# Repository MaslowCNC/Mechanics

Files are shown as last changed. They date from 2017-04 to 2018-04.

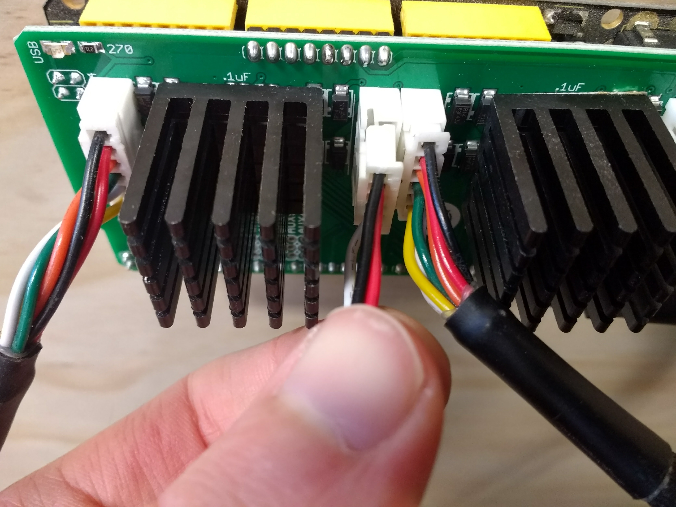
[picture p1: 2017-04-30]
Documentation/Installing The Z-Axis/Plug Into Controler.jpg

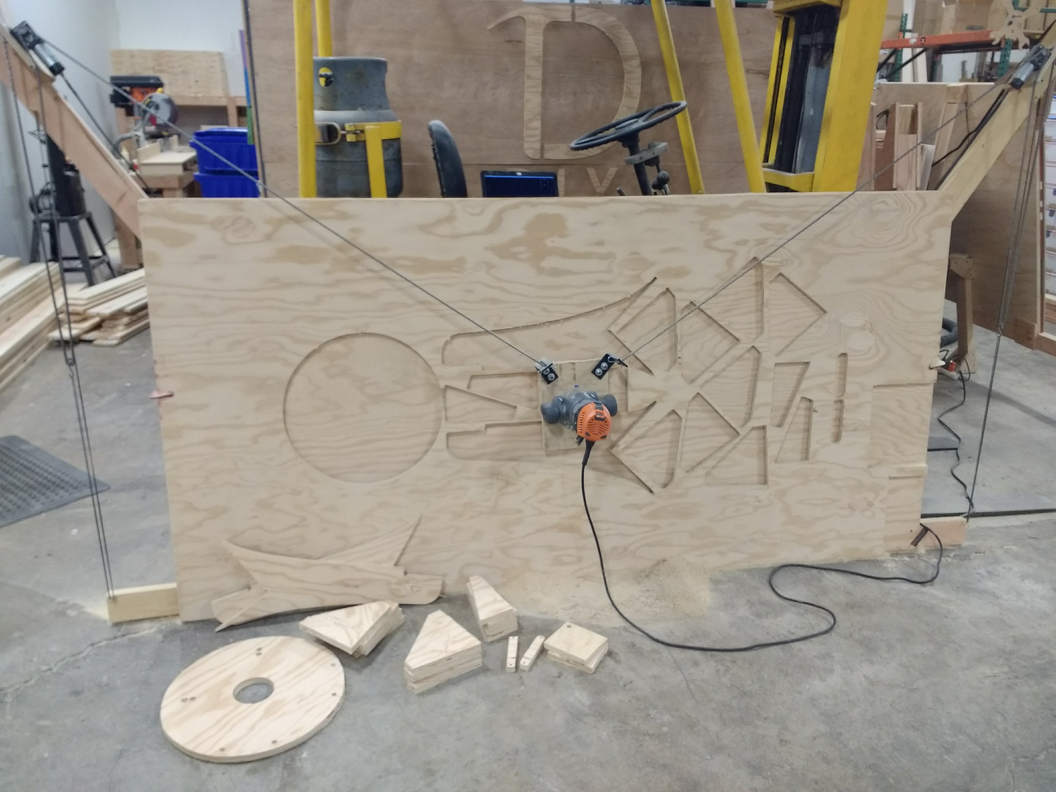
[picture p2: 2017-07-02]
Documentation/Cutting Parts With Temporary Frame/All Parts Cut.jpg

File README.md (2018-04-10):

# Maslow CAD

The digital design files for the Maslow CNC Machine

===

Digital Design Files

The official latest version of the design has moved from Sketchup into OnShape, a web based
parametric CAD program which lets us more easily modify and adadpt the design than Sketchup
did. 

You can find the OnShape model for the default frame here:

[Default Frame OnShape Model](https://cad.onshape.com/documents/bb4070d4347a04156066aecd/w/cc700f50fb591efdcf3dff27/e/5fe97348d45b2bf22a29a1ce)

You can find the OnShape model for the bolt together frame here:

[Bolt Together Frame OnShape Model](https://cad.onshape.com/documents/541f931ef1cd300726f54cf3/w/2e46e46e415d8c274b77c05c/e/bbd5cb914ffed6d673f649a3)

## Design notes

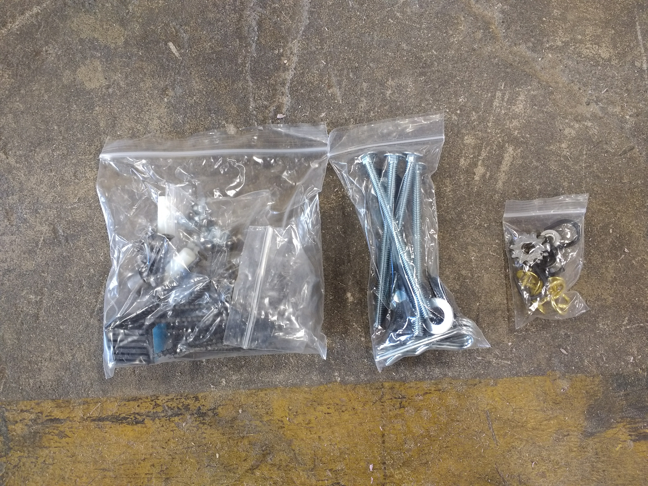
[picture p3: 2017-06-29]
Documentation/Hardware Bags.jpg

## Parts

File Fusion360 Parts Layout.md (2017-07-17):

# Unofficial Fusion360 parts file
---  
It was mentioned that the Autodesk folks might be making a post-processor for MaslowCNC (GC). In preperation for optimization of Fusion360 for use with MaslowCNC I've created and shared a Fusion360 Project that incorporates and extends the 'All_Parts_Laid_Out.svg' document, designed for cutting MaslowCNC from a single sheet of plywood, and hope to continue to update this Fusion360 Project file to allow easier creation of additional MaslowCNCs and to make it easier for folks to begin building and working with Fusion360 to design things to be built with MaslowCNC.

Experienced Fusion 360 users and/or active MaslowCNC Developers are welcome to contact me in order to be added as collaborators on this project within the Fusion 360 Cloud platform.
  
---
### [MaslowCNC Beta3 Parts](http://a360.co/2sV4YRd)
---
  
### Updated (7/7/17): 
* Parts Sketch, suitable for cutting all parts from a single piece of Plywood.
* Seperate 'extrusions' for each part
* Simple Component Paths: The Bare minimum to make the shapes and cuts necessary for the MaslowCNC parts. 
* Advanced Component Paths: All part paths, Pockets for the Sled mounting bolts, the Rigid Router's own plastic sled, engraved angle braces.
  
### To be added:  
  * More accurate machine settings (Feeds and Speeds) for all paths.
  * Roundover cuts for the Advanced sled, using a V-Bit
---  

More information: [Fusion360 with MaslowCNC](https://github.com/MaslowCNC/GroundControl/wiki/Fusion360-with-MaslowCNC)

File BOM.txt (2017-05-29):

Frame BOM:

8  x Cup Hooks
6  x 1.5mm Pullies
2  x S-hooks
2  x Idler Sprockets
2  x Drive Sprockets
2  x Motor/Gearbox/Encoder (291:1 reduction gearbox with worm gear to prevent back driving motor, 30kg/cm torque, 20 rpm, 12 volts)
2  x Motor Mounts
2  x 2.5"x3" U-Bolts
2  x Chain Brackets
2  x Chain Bracket Bolts
4  x Cotter Pins
25 x Wood Screws
3M x Stretchy Tensioning Cord
2  x 11' #25 Roller Chain

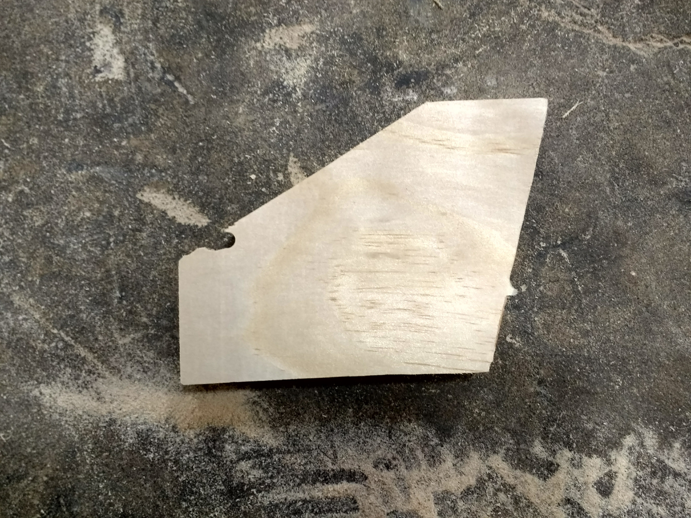
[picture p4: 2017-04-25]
Documentation/Cutting Parts With Temporary Frame/Part With Gash.jpg

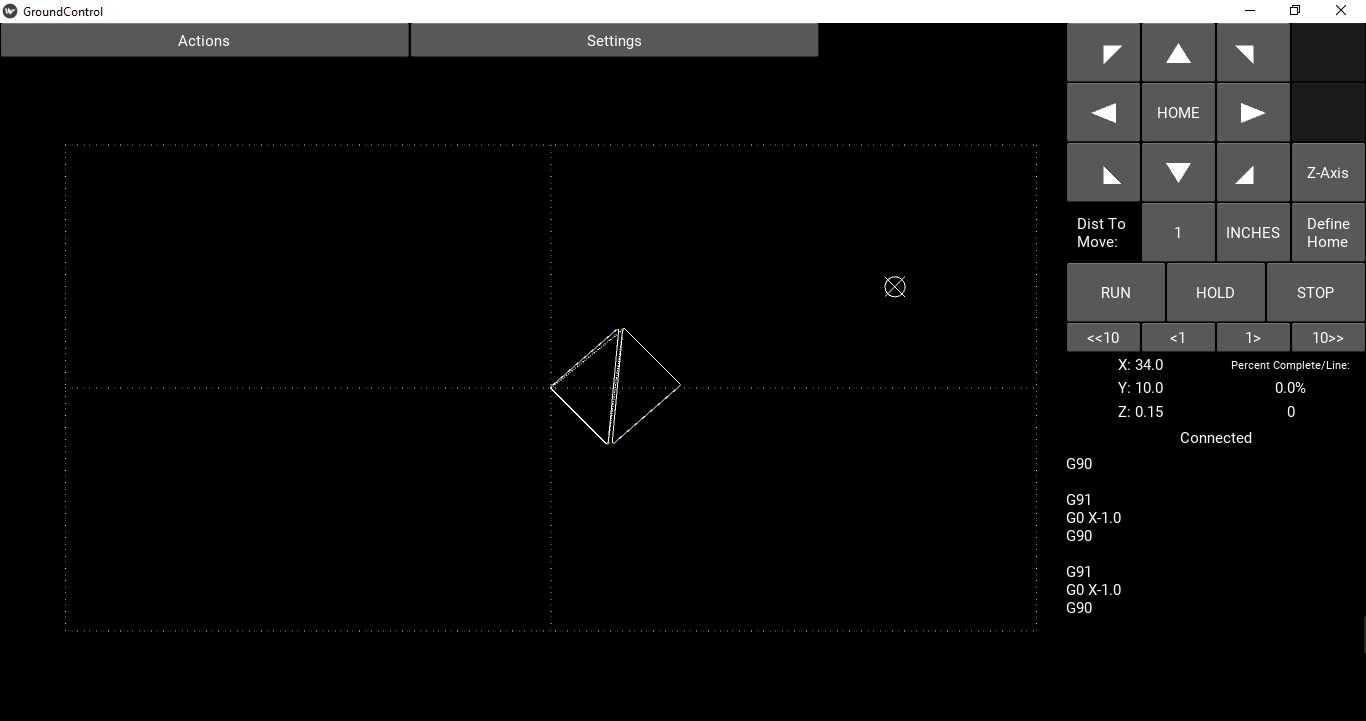
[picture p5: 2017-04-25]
Documentation/Cutting Parts With Temporary Frame/Move Machine Over.JPG

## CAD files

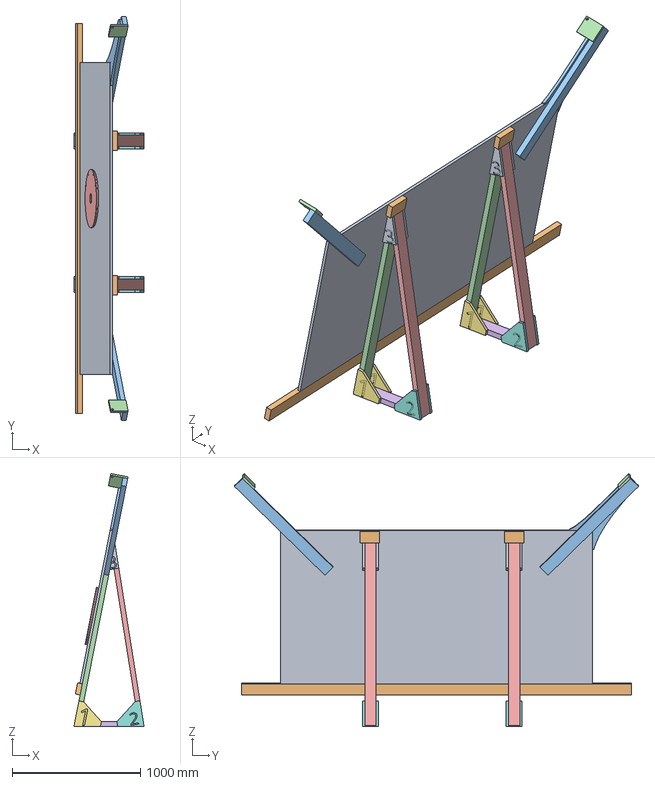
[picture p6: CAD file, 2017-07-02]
Maslow Frame.step
548.2 x 3156.8 x 1976.4 mm

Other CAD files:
Hardware/Bracket A.skp
Hardware/Bracket B.skp
Hardware/Bracket C.skp
Maslow Frame.stl
Maslow Frame.x_t
Testing and Calibration/6 Inch Square Test Shape.skp

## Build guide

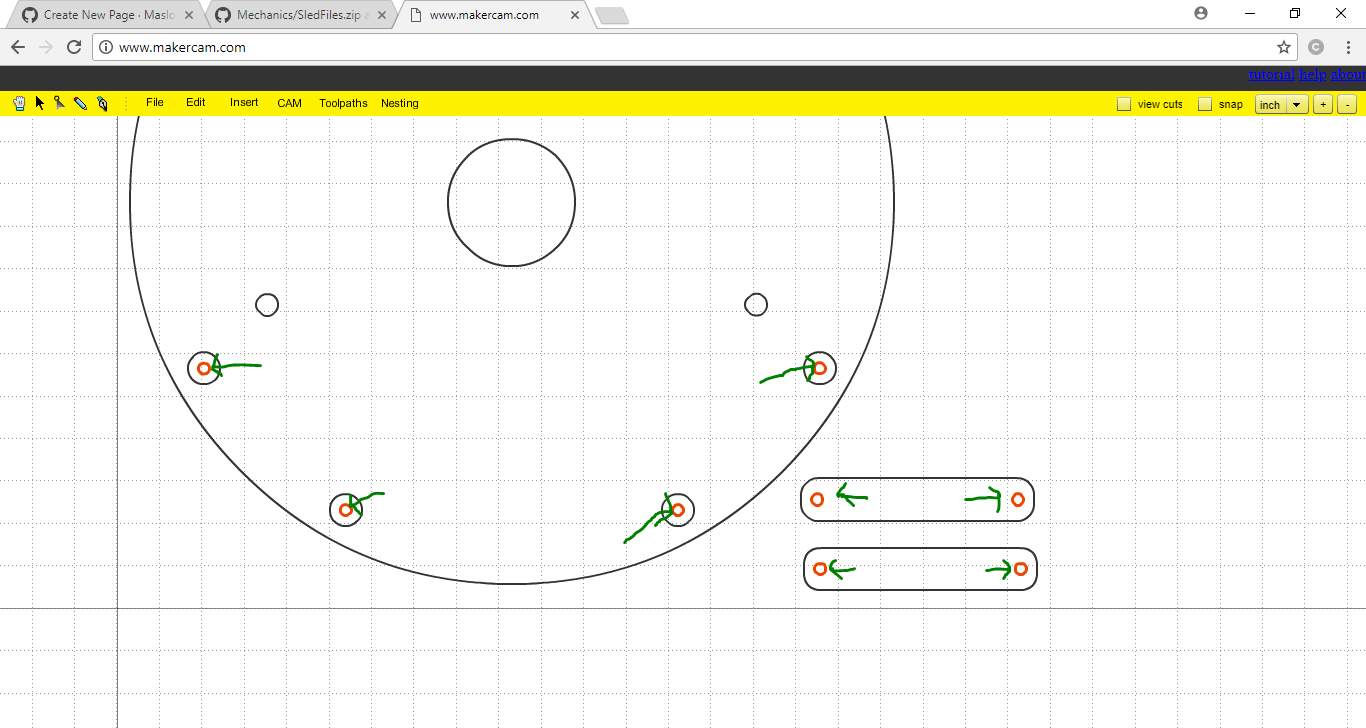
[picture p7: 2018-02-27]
Documentation/MakerCAM/Eight holes.PNG

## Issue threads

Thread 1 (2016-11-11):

Motor/Gearbox/Encoder - Specific Requirements

iceblu3710, 2016-11-11:
What are your requirements for the motor?

* RPM at shaft
* Running torque
* Min effective CRP at shaft

NeoTheFox, 2017-04-01:
Yes, some details would be nice.

mrfugu, 2017-07-13:
motor details have been documented.
this issue probably can be closed.

Closed 2017-07-13.

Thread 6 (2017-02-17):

Make motor placement more defined

BarbourSmith, 2017-02-17:
Where to place the motor on the motor mounts is a little unclear. I would like to add recesses for the screws to indicate where they should go and a second hole which the chain passes through after going over the sprocket to encourage consistent placement.

blsteinhauer88, 2017-03-29:
Awsome idea!

mrfugu, 2017-07-13:
New Arm Design appears to resolve this.

Closed 2017-07-13.

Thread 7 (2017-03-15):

Motor_Mount.svg file seems wrong.

blurfl, 2017-03-15:
MakerCam and InkScape don't seem to find an outline in the file. Was it created from the appropriate view?

blurfl, 2017-03-15:
Here's a file that looks OK in MakerCam and InkScape.
[Motor_Mount.svg.zip](https://github.com/MaslowCNC/Mechanics/files/846039/Motor_Mount.svg.zip)

mnelson78, 2017-03-15:
I opened it in Illustrator and it looks good now.

BarbourSmith, 2017-03-15:
Does PR #8 look like it fixed the issue?

blurfl, 2017-03-15:
MakerCam is happy with them all. InkScape sees the stroke as 90px wide, so renders them with hugely fat lines :(
Should there be one for the sled, as well?

davidelang, 2017-03-16:
when doing CAD work in .svg (inkscape and others), you should always use an
extremely thin line, otherwise you run the risk of the machine trying to cut
both sides of the line.

On Wed, 15 Mar 2017, Scott Smith wrote:

> MakerCam is happy with them all. InkScape sees the stroke as 90px wide, so renders them with hugely fat lines :(
> Should there be one for the sled, as well?

BarbourSmith, 2017-03-16:
@davidlang I agree. The line exporter in sketchup doesn't seem happy exporting a line thinner than .05 in which isn't exactly narrow, but it is better than it was. I think I may need to download inkscape tomorrow to make them truly hair thin.

I've also added a file for the sled.

Do we feel good about merging PR #8 as is for now?

blurfl, 2017-03-16:
Bar,
 I’m using the .SVG exporter mentioned to Hannah by RifleSpiral , 20dThu Feb 23 2017 05:14:46 <http://www.maslowcnc.com/forums/#!/no-judgement:sketchup-is-friend-not-foe/theres-a-branch-on-github> and it is willing to do 3.54px (on the Mac I’m using…). No special setup, just using the 1mm defaults for line size.

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

blurfl, 2017-03-16:
Bar,
The motor_mount.svg file was not updated with the rest of them, it is still the fat one. Other than that, ready to merge.

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

davidelang, 2017-03-16:
It sounds like the right thing to do, so no reason not to merge the fixes

David Lang

k

BarbourSmith, 2017-03-16:
Thanks for the advice everyone. I'll make everything as close to zero width as I can first thing tomorrow. Yall are also welcome to make pull requests for this kind of thing if it's faster

Closed 2017-03-15.

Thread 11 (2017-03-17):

Missing SVG file for brick holding bracket on sled

mnelson78, 2017-03-17:
There is not an SVG file for the bracket that holds the bricks onto the sled, and there should be.

mnelson78, 2017-03-20:
Bracket is now posted.

Closed 2017-03-20.

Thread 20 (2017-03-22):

Reduce friction between sled and cutting surface

BarbourSmith, 2017-03-22:
I suggested in [this video](https://www.youtube.com/watch?v=5pmNkcbVRkE) that we need to reduce the friction between the sled surface and the wood being cut.

In the video I suggested that we could reduce the friction by pocketing out some of the area under the sled. It has been pointed out (very correctly) that friction has more to do with the weight of the sled, than it does with the surface area so creating a pocket can't actually reduce the friction. I think there is still some room to play with the idea of pockets under the sled for either improved dust collection or to distribute the weight differently because drag toward the edges of the sled produces greater torque to twist the sled than drag near the center.

The two factors which affect friction are the coefficient of friction and the weight of the sled.

We can reduce the coefficient of friction by using a slippery material like nylon or HDPE to make our sleds. I think that's a fantastic idea, but since it's not available to everyone I'd like to look for other solutions in the meantime.

Reducing the weight of the sled is a good option. We don't really need to reduce the weight, only the force excreted by the sled on the material being cut, which we can control by adjusting the tilt of the machine. The current angle was decided back when we were using a much smaller less stable sled. I think our new larger sled could handle a much lower angle and still be stable.

davidelang, 2017-03-22:
I've been wondering about the angle, I figured I'd ask the beta testers to do
some experimentation with steeper angles once we started getting several of them
online.

That should let the sled be lighter as well (while keeping the same tension on
the chains), which would also open up the possibility of faster movements for
the design (either via motors with different gearing or larger sprockets)

mikberge, 2017-03-25:
first thing it come my mind, something cheap and easy to find....one cutting board! made with plastic similar to nylon or teflon .made to be durable and glide well. i think about two option , same form as the sled or many pocket under the sled plywood to insert many disc of cutting board strategicly these kind of plastic can be cut with the maslow

mikberge, 2017-03-25:
https://www.walmart.ca/en/ip/mainstays-pp-cutting-board/6000196138411

davidelang, 2017-03-25:
or this one that was posted a while ago

https://www.samsclub.com/sams/bakers-chefs-commercial-cutting-board-15-x-20/126035.ip?xid=plp:product:1:1

k

Seventhram, 2017-04-02:
Hi, I'm a beta tester.  I'm in the process of building my frame. I was a little concerned about the angle as well. I built my frame to be adjustable (using bolts on the top and bottom). Currently I have mine built to a 15 deg angle. I like the cutting board as a sled idea. I purchased a walmart cutting board, its rectangular, 20"x15"x3/8"thk. I'll most likely cut it to be more of an elliptical shape. Pic's to follow.

BarbourSmith, 2017-04-02:
Let us know what you learn!

buzz4209, 2017-04-03:
Many woodworking projects use melamine coated plywood or OSB for reducing friction. It's cheap and readily available.  Chamfering  the edges should be done too, as sharp corners may have a tendency to dig in and catch on any roughness present in your materials.

The cutting board idea is a good one, but I'm not sure the 1/2 inch thick polypropylene ones will work out long term. I'd worry about rigidity and durability based on the ones I have in my kitchen. :-) Best would be Corian (countertop type material) it's harder and slicker. Polypropylene will wear (scratch) much more readily than corian or melamine. It's generally a softer material. Unfortunately the Corian cutting boards are harder to find. I think Menards in the US often has them.

rb0087, 2017-04-08:
I think that ball transfer bearings would be the ideal solution to this problem, but it would potentially add a bit to the cost. Still, I think that it's an idea worth considering, because it would eliminate the issue of sliding friction with the wood. Instead, you would have rolling friction with the wood, and mostly rolling friction between steel ball bearings inside. The issue of it catching on the edges would also be largely eliminated. I think that you could source suitable ones for around $2 each in bulk, and if the design used ~10 of them, it wouldn't be a huge expense. It's also quite possible that some creative minds could think of a cheaper alternative that's inspired by this. Other than cost, the complication with this idea is that you would need enough of these to make sure that previous cuts in the plywood don't cause problems. If you had a perfect surface, 3 would be enough, but it would obviously cause problems if any of the 3 were going over dips in the plywood.

With the current design, regardless of what material the base is made out of, or what shape you have, with a flat base bearing on the surface, you'll still have sliding friction, and it will be difficult to predict because one of the materials is obviously plywood. Moisture content of the wood, the species/grade of the wood, etc. will all have an effect. When you have wood-wood, and wood on many plastics, you'll also see stick-slip behavior, which will make the motion difficult to control smoothly. This paper has some great info on the subject: [http://catalog.lib.kyushu-u.ac.jp/handle/2324/23785/p147.pdf](url) .

Also, if you do continue down the route of using a solid base like you currently have, I'd just like to point out that the shape does matter, regardless of the fact that you won't see the surface area anywhere in a simple friction equation. If this were lying flat on a table, and the forces were being applied right at the base, it might not, but in this case, the reaction forces at different points on the base will be different depending on how hard the chains are pulling (which will be applying a moment because the forces aren't directly in-plane), where the CG is, what the cutting force is and at what depth, what the grain direction is and what local imperfections are present, etc.  With uneven reaction forces comes uneven friction, which could be higher than a simple F=mu*m*g*sin(theta) would give you, and could be causing the base to rotate about its' center of gravity, which would cause positional errors at the cutting bit if it isn't the center of gravity.  Anyway, my main point is that it's not a simple situation, so I would trust your intuition that the shape is important. I think there's probably a bit of performance that could be gained by optimizing the shape.

BarbourSmith, 2017-04-08:
Thank you for that clearly well thought out and on point answer. I agree with everything you said.

The idea that the shape matters is I think an especially important one. The shape is a variable that we have a lot of flexibility to play with. We have the ability to play with not only the perimeter shape of the sled, but also the contact surface area by creating pockets.

The paper is quite insightful. Thank you for linking that. I thought that this graph which shows the "stick-slip" behavior of different plastic types was particularly interesting:
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
davidelang, 2017-11-14:
On Tue, 14 Nov 2017, Josh Martin wrote:

> For slickness, laminate flooring is cheap, or some self stick vinyl sheet would be ideal.

or UHMW plastic (available as cutting boards cheaply)

> Ball bearing casters can be had quite cheaply (~$1 on amazon) and come in nylon and steel. They can be inset from the bottom to minimize height.

they will have a tendency to fall in to areas you've already cut.

> Add a few coats of urethane to the bottom of your sled?

yes

> An air hockey table sled would be cool? (reverse your vacuum, it doesn't work that well anyway :P).

would be very cool.

> Remove the weights, add a bungee to the bottom center of the frame to the sled, and tilt the machine more.  It should provide comparable stability for cutting, but a better coefficient for movement.

see the discussion about adding a third motor that we had a few days ago, it
turns out this isn't nearly as easy as it sounds at first. When you are cutting
near the bottom corners, the bungee cord would be pulling in the wrong
direction, making a bad problem worse.

matthewkleinmann, 2017-11-15:
Some thoughts.  I don't have a router yet, but I have built a lot of things..

1) The ball bearings.  I am not a fan of this idea because as the piece the sled is gliding over starts to get tracks touted out of it, I would fear that unless the sled is perfectly balanced one or more of the bearings might get stuck or skip as it attempts to cross the void.

2) The cutting board.  I like the concept, but perhaps try making the sled out of aircraft grade plywood or even aluminum.  Yes, it is more expensive.

3) I am looking forward to hearing how the packing tape worked out.  Thin and inexpensive.  Perhaps that over aluminum as I think it would adhere better to a totally flat surface.

4) I worked on an experiment once and we bought thin adhesive backed teflon.  I don't recall the source or the price.  I suspect it was not inexpensive, but it was a really good material. and this use would only require a small amount of it.  Again, over wood or aluminum.

5) My last thought, more out of the box and harder to effect would be to make the sled something like an air hockey table powered by a shop vac.  This would give you some degree of weirdness in the Z axis, but I suspect for the vast bulk of the projects people are building with this router, that is acceptable.  For the things I would like to build, the Z axis is pretty much in or out.  FWIW, I got enamored with the air hockey idea pondering building extension feed tables for my planer.

davidelang, 2017-11-15:
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

This could also have problems going over earlier cuts (just like the bearings
approach)

servant74, 2017-11-15:
Another approach, is to use teflon.  Contact your local plastics supplier,
and get some thin Teflon or PTFE sheets that have been acid etched.
This will allow epoxy to attach well and stay.  Mix your favorite epoxy and
cover the sled bottom, and put on the sheet (etched side toward the epoxy)
and leave under some amount of compression (to keep things from springing
apart while the epoxy cures).
The sled can be cut/trimmed with normal tools to make way for smooth edges
etc.  Teflon is really pretty soft.

This was used when my Dad worked for Bell Helicopter on some of the parts.
They used high temp epoxy and put it in clamps then in an autoclave under
pressure.  But hey, it was for aerospace use, so money was no object.  We
used their cutoffs/scraps of Teflon like this to make furniture slides for
use around our home.  It worked well.

From a quick look online, the acid etched PTFE that is thin (say .02
inches) runs about $1.80/sq ft USD.  There may be minimum orders plus
shipping, but such is life ordering industrial goods.  Hopefully you can
find some without to much overhead involved.

davidelang, 2017-11-15:
On Wed, 15 Nov 2017, Jack in TN wrote:

> Teflon is really pretty soft.

I would worry that the Teflon will get chewed up by the edges of the wood and
chips (note that I worry about a lot of things)

matthewkleinmann, 2017-11-15:
David: On the air levitated approach, I had the same thought about the air levitated sled, but if you look at an air hockey table, most of the holes are uncovered most of the time.  For me the show stopper there is how complicated it is.

On the teflon, the stuff we had was tough.  It was akin to the stuff they use in dryer bearings.  Not quite that heavy but definitely tough stuff.

blurfl, 2018-01-10:
This is a valuable discussion, but not really an issue. Is there a way to move this to the forum or the
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

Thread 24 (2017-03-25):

Building temp frame step 10

sanenerd, 2017-03-25:
docs say
Step 10: Attach Cup Hook to top of Plywood Sheet

Attach 1 Cup Hook (found in the Small Hardware Bag) to the top left corner of the sheet of plywood below and slightly to the right of the motor shaft.

Pic show attaching to 2x4.. I assume photo is right

PS. I am sorry if I am putting this in the wrong place

BarbourSmith, 2017-03-25:
Great catch!

This is absolutely the right place!

The picture is correct, I'll change the text right now (you also have the ability to edit it directly using the "Edit" button in the right corner if you want)

BarbourSmith, 2017-03-29:
I'm going to close this if that's ok. I think it should be up to date. Thank you again for pointing that out!

Closed 2017-03-29.

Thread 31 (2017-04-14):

Unclear router description and features

jbarchuk, 2017-04-14:
Re; https://github.com/MaslowCNC/Mechanics/wiki/More-Photos
Bar, your page with the Bosch router explains a lot and the pics are excellent but might be confusing to users. First, it doesn't include a specific model number. I managed to track it down by the nameplate pic but there might still be oddities. These manufacturers build tools with different features and varying part numbers, and sometimes different features/numbers for different world regions.
Second, more importantly, is that the first pic might be misleading. That router is AAMOF the only one I've seen that has 'fixed base adjustable height' AND plunge style 'travel stops' features. It does that by giving the adjustment rod a latch mechanism that slips into the rotating 'stops wheel.' A user might see that wheel, see it on another router, and not understand the lack of the notch at the bottom of the adjustment rod, and get a router that can't do what's needed.
I think those pics should be moved to the 'router reviews' page with an explanation that it's a 'dual style' router suitable for Maslow's needs but unusual/different from other routers.

GeroBH, 2017-04-15:
@jbarchuk All pictures was originally here:   https://github.com/MaslowCNC/Mechanics/wiki/Tested-Routers-List
I admit, too many pics. Will try to make that more compact. They were moved to 'More-Photos' to make the router list better to overview.
Behind the model number there, it is mentioned that this router is not recommended and not tested. The 'not tested' will be removed today, because it is moving and it will cut. The 'not recommended' will remain, as this is one heavy beast (7kg without bricks and sled), to high, bringing the centre of gravity far over the sled. Moving it to the top edge of the cutting sheet made one of my motor mounts bend and a chain jump over the sprockets. It is sure not in the line of the goal 'Make it possible for everyone to have a Maslow', more on the line of testing how far you can go to reach the limits of the design. May I add more pictures of how the Z-Axis is mounted?

BarbourSmith, 2017-04-16:
I think more pictures clarifying how the z-axis is mounted would be a great thing. I think @jbarchuk is right that we should make it clear that it's a unique router type. @jbarchuk do you think it would be possible to make it clear without adding more pictures, just to keep the router review section clean? Hopefully we will soon have a number of routers listed there and I'm worried about it becoming crowded.

jbarchuk, 2017-04-17:
I didn't mean to give the idea that there were 'too many' pics. Absolutely
not at all. The more the better especially around the z-adjustment
hardware! Beyond that all these routers are just a motor and base.On one
level, there are two kinds of users. The first user has a router and needs
to decide if it'll work for Maslow. The second kind has particular projects
and needs in mind, and needs to pick a router.
On another level there are similarly two kinds of users. One (me for
example) has a very narrow-specific task, and they need to pick the router
with the best features for that task. The other user has potentially many
different kinds of projects in mind, has no router at all, and needs to
pick one with a wide enough range of variables that could meet all of those
tasks. For those folks there's more compromise required because there will
be no 'perfect' router.
There's no way to describe, show, and test every router on every material
under every condition. The best a web page of pics and descriptions can do
is say 'it does [this] really well and [that] average to poor.' It's up to
the individual user to decide if what they have will do what they need, or
which one they need to get to do what they need.
Again (heeere we go again :) ) this is where m00t and wiki are -not- good
software for these kinds of displays, descriptions and discussions. Yes,
one huge long page that has every photo and detail of every router can do
it, it's just -easier- to read one page about one router and not have to
bother with the others.
-More- information can -never- be a bad thing!!
Heck the 'too big too heavy' thing that you experienced Gero might be a
deal -maker- for someone who wants to drive a 1" bit through 1" oak!
Whether the -frame- is a little too weak to handle the high end of the
power bell curve is a different issue, but it's exactly those kinds of
tests that that user wants to read about. It's -very- easy to make the
frame stronger if necessary, and the chains and motors are certainly
already strong enough. As has been seen the exact frame build style is not
cast in stone. The intent of the Maslow concept is not 'this design can do
any and every task,' but that it can be tweaked and recast to do many
different specific tasks.
A related topic, whether the style of g-code generation of a particular
software, and exact firmware operation is suitable for any task is up in
the air. It's possible that there will be different power ranges that one
style works best for lightweight stuff and a different style works better
for heavy stuff.
This is all very similar to how plain router (or any power or unpowered
tool) operation works in real life. It takes practice and experience to
make any tool perform a task. Folks want to read about specific experiences
to see if things will perform nicely for what -they- want to do. If a
router is out of the range of what a user needs they'll have to decide if
the tweaks will be enough to bring it in range whether it's shallower cuts
or slower cuts or a different kind of bit or even a different frame angle.

On Sun, Apr 16, 2017 at 2:19 PM, BarbourSmith <notifications@github.com>
wrote:

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

GeroBH, 2017-04-17:
Thank for the comments. I could add something like a watermark with model and type on the picture itself, like GOF 2000 CE / Fixed Base. What do you think?

BarbourSmith, 2017-04-17:
I think it looks great. I didn't realize how big that router is until seeing the z-axis attached. Wow, it's huge! Overall, I think that the changes look great. Thank you for the update.

mrfugu, 2017-07-15:
I gave each router their own wiki page linked from the 'tested routers' page, this issue can probably be closed.

Closed 2017-07-17.

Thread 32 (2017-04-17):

Front Arms point needs rounding

mnelson78, 2017-04-17:
The front arms file goes to a sharp point.  This is the point that sits on the top of the sheet of plywood and points horizontally.  When cut out in plywood the point just chips away.  This also creates a weak point that is easily broken during the building of the arms.  I suggest rounding this point, perhaps a 1" radius?

BarbourSmith, 2017-04-17:
Great suggestion and an easy change

mrfugu, 2017-06-21:
I'm happy to make this change to the Fusion360 file I've created (http://a360.co/2sLJASm).

If you'd like, I can round that corner over and export out to a new Arm_Front.svg as well?

BarbourSmith, 2017-06-21:
@mrfugu, that would be great if you want to take that on! 👍 👍

I've been working on a frame redesign that dramatically reduces the part count and I just updated the github with the new versions of all the files so be sure to work from the latest files so we don't waste your time.

Cool Fusion model!

davidelang, 2017-06-21:
It's really nice with an update simplifies construction :-)

mrfugu, 2017-06-21:
Hey thanks, glad to assist.  I'll update the fusion project with your new SVGs 1st, then make any changes needed. will update once it's live.

mrfugu, 2017-06-21:
I've created Pull Reqs with the updated versions of 'All_Parts_Laid_Out' and "NewArmShape' incorporating a 3mm fillet to round over the sharp points in the arm, and widened the Brick Holder holes just slightly (from 6 to 7 mm) to allow Fusion360, in particular, to easily program those holes with a standard 1/4" plunge bit.

mrfugu, 2017-07-13:
this issue can be closed.

BarbourSmith, 2017-07-13:
@mrfugu  Thank you for flagging all of these

mrfugu, 2017-07-13:
no sweat. rock on!

Closed 2017-07-13.

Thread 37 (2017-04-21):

'Using the Temporary Frame to Cut Parts' has two Section 9's and no Section 10

blurfl, 2017-04-21:
Need to renumber.

BarbourSmith, 2017-04-21:
Great catch!

Feel free to edit the page, or I can take care of it first thing in the morning.

BarbourSmith, 2017-04-21:
Two 9's and no 10!

Closed 2017-04-21.

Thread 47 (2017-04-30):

Z-Axis Help

Seventhram, 2017-04-30:
Can someone please tell me which port to plug the Z-Axis cable too.

Can someone please post a picture of the mounting of their Z-Axis.

Suggestions on the best way to remove the knob and dial on a Ridgid R2200 router.

BarbourSmith, 2017-04-30:
Great questions, thanks for pointing that there needed to be a clear guide to that process. There is now a guide [here](https://github.com/MaslowCNC/Mechanics/wiki/How-To-Assemble-The-Z-Axis).

Let me know how I can make it better. 👍

Closed 2017-04-30.

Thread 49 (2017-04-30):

Design braces to be shapes which can't be reversed

BarbourSmith, 2017-04-30:
When assembling the legs it can be hard to tell which way the braces go. This could be fixed by making them more distinct shapes than triangles.

mrfugu, 2017-06-21:
Similar to my response to Issue #32 , I'm happy to edit my Fusion360 file and export updated .svgs for Angle Braces 4 and 5.

mrfugu, 2017-07-13:
Angle Braces 4 and 5 no longer exist.
this issue can be closed.

Closed 2017-07-13.

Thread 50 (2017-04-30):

Make cutouts for bit in arms larger

BarbourSmith, 2017-04-30:
The cutouts to allow the arms to have interior right angles where the motor plates mount need to be made larger for 1/4 inch bits

mrfugu, 2017-07-13:
this issue can be closed.

Closed 2017-07-13.

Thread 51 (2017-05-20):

Chain link height

ronbutterfield, 2017-05-20:
Please add a note to step 18, that the height the chain is attached to the sled should match the center of gravity of the router/sled assembly.  This may need to be adjusted for cutting very thick or thin materials.

davidelang, 2017-05-20:
and ideally you want the chain to be straight, so you want the motors out far
enough for your 'standard' material (say an inch from the frame + what's needed
for the center of gravity for the sled)

BarbourSmith, 2017-05-23:
That's a great point, it should be clearer.

Feel free to edit the wiki page directly when you come across something like that, or I can.

blurfl, 2018-01-10:
Has this been accomplished? If not, volunteers? 😁

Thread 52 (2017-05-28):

Detailed specs for motors and encoders

rodrigogoncalves, 2017-05-28:
Hi, is the [BOM](https://github.com/MaslowCNC/Mechanics/blob/master/BOM.txt) the official specs of the parts used? I'd like to know the makes and specs for the motors and encoders. Thanks

davidelang, 2017-05-28:
the motors are custom built, they have a 291:1 worm gear with a 7-line encoder
on the motor, resulting in 8148 pulses/rev of the output shaft, they have a
final drive torque of 30Kg/cm and turn at 20 rpm

Enjoying28, 2017-06-06:
I wonder if we can make a machine with these materials.

GM4632-370 DC 12V 30RPM High torque Turbo Encoder Motor Worm Geared Motor Reducer Motor
http://a.co/6l5dS2B
Browning 25B10 Minimum Bore Roller Chain Sprocket, Single Strand, Steel, 1/4" Stocked Bore, 10 Teeth
http://a.co/3dT9nYc
25 Roller Chain 50 Feet with 5 Connecting Links
http://a.co/0Qzel3k
Makeblock MegaPi - Born to Motion Control for Maker and Geek
http://a.co/iL2OnRn
Makeblock Megapi Encoder/DC Motor Driver
http://a.co/3wgzsT6
NEWSTYLE 12v 30a Dc Universal Regulated Switching Power Supply 360w for CCTV, Radio, Computer Project
http://a.co/7Ea39eI

maybe would have to edit the step factor

davidelang, 2017-06-06:
looks plausable, I'll point out that you are driving three motors which take
<0.5A each, so your 30A power supply is drastic overkill

The motor's rated torque is less than the maslow motors, but the worst that will
happen is that this means you have to go slower.

there will probably be some software changes needed to make the software run on
that board (and it's not clear from the Amazon page how much flash is on that
board, so double check that there is enough space.

David Lang

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

mrfugu, 2017-07-13:
an optional/equivalent parts list has been created.
this issue can be closed.

Closed 2017-07-13.

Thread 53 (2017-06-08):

All_Parts_Laid_Out.svg AngleBrace1 error

mrfugu, 2017-06-08:
In the file "All_Parts_Laid_Out.svg" the patterns (2) for the part called 'AngleBrace1.svg' has a sub-mm inconsistency in its long sides.

This doesn't seem to exist in the "AngleBrace1.svg' file itself, just the "All_Parts_Laid_Out.svg" file. It's minor, but probably adds unnecessary complexity to the tool paths generated for this part using this consolidated file.

-mrfugu

mrfugu, 2017-06-08:
Correction: This error appears on the long 90 deg edge of the AngleBrace1 shape, which appears 4x in the " "All_Parts_Laid_Out.svg" file

BarbourSmith, 2017-06-08:
Good catch! Thanks for noticing that. If you want to make a pull request which fixes it, I would love to merge it. If not I'll look into correcting the issue.

mrfugu, 2017-06-08:
Cool, will do it now.

mrfugu, 2017-06-08:
this is my 1st Github contribution, apologies if I made a mess of it.

mrfugu, 2017-06-08:
Well, the file is in my post, but it reads to me like i requested a merge of recently changed files as well, not my intent.

BarbourSmith, 2017-06-08:
😀 You ARE helping!

It seems like maybe a bunch of other files got wrapped up in the pull request for some reason, maybe give signing [the guest book](http://www.maslowcnc.com/howtocontribute) a go to test the process out

mrfugu, 2017-06-08:
Hey, thanks!

	Sorry about that, I’ll read more instructions before any future contributions, hope I didn’t make too big of a mess!

	Cheers,

Robert Crecine
429 1st Ave
Suite 8
Pittsburgh, PA 15219
412-580-8618

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

BarbourSmith, 2017-06-08:
The beautiful thing about Git Hub is it's virtually impossible to mess anything up. Every change is logged and reversible so you can pretty much always go for it! 👍 👍

mrfugu, 2017-06-19:
Ok, I think I got it right this time, I re-submitted the corrected 'All_Parts_Laid_Out.svg' file.

BarbourSmith, 2017-06-19:
Just merged it. Fantastic work! Thank you.
👍 👍 👍

Closed 2017-06-19.

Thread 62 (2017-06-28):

All parts SVG missing parts

ladyhawke13, 2017-06-28:
Shame on me for not going through the step of verifying - the All parts laid out SVG is missing the back piece of the arms, as well the two middle angle braces(the non-triangular ones). Also missing the SVG for those individual parts.

For non-beta users a measured diagram with all plywood and 2x4 parts numbered would be very helpful(speaking as someone who used to help with flat pack assembled furniture instructions!). I'll be winging it with scraps and likely using my jigsaw for the back arm piece, as I'd started disassembling my temporary frame before realizing that I was missing things.

BarbourSmith, 2017-06-28:
You caught me right in the middle of re-writing the instructions to not need those parts.

The new simplified design uses a 2x4 for the back of the arm part, and removes the middle brace from the legs to simplify construction.

I'll be re-writing the written instructions and taking pictures today.

ladyhawke13, 2017-06-28:
Leave it to me to pull at the wrong time! I have the frame supports together well enough, I just need to do the arms. I'll be retrieving my jigsaw from a different project site tomorrow and hopefully can get those cut out Friday.

BarbourSmith, 2017-06-28:
The new arms are mostly 2x4s, with the face plate mostly there for decorative reasons, You can really just use the 2x4s without bothering to cut the front parts if you want.

It will be more clear once I get the instructions written 😀

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

ladyhawke13, 2017-06-29:
Ahh, gotcha! I definitely have more than enough 2x4 scraps floating around to do that. I have the front pieces of the arms, just not the back. So easily enough sorted :)

mrfugu, 2017-07-13:
this issue can be closed.

Closed 2017-07-13.

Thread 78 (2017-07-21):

Source for Motor mounts

JDogHerman, 2017-07-21:
In the BOM I don't see a source for the motor mounts. Anyone have a suggestion where these can be acquired?

The measurements seem to have an opening of 28x40mm

JDogHerman, 2017-07-21:
I found a part that has a compatable opening.

I searched for

> GW31ZY GW370 DC Geared Motor Block Motor bracket Horizontal mount Motor Mount

Several showed up for less than $5.

Hopefully this will help someone else.

Closed 2017-07-21.

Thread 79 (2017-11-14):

Avoiding tearing down the temporary frame

skiz, 2017-11-14:
I was able to avoid removing most of the temporary frame (including all of the electronics, motors, etc) by taking a few precautionary steps along the way.  I have also avoided adding the additional arm facades, as I know my arms are both 20" out at 45 degrees.  I may revisit this at a later time, but it saved quite a bit of work and lots of recalibration time not having to deal with tearing everything apart.

1. Unplug anything that could move
1. Detach the sled (and z-axis if you have one), and use the pins to keep the chain attached on the gears (as close to the gear as possible).
1. Unhook the bungees from the tensioners, and safely remove and store the tensioners/hooks/gears.
1. unscrew the lower temporary legs as per the instructions
1. measure and screw the 2 6" blocks to the back/top of the frame.
1. build the permanent legs and mount per the instructions
1. simply hook back up the tensioners and remove the pins from the chain.

I figured this may save someone else some time, but being an "unofficial" hack, I'm adding it here.

BarbourSmith, 2017-11-14:
I am going to fully revisit the frame design and build process before batch three and I will try to incorporate these ideas, thanks for the tips!

blurfl, 2018-01-10:
Good suggestions, have they been incorporated? Is this issue needed as a 'to do' item?

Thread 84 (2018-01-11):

Why does the shop have a picture of z-axis mounted sideways on a motor mounting plate?

GeroBH, 2018-01-11:
Just curious and confused.
http://www.maslowcnc.com/store/z-axis
Middle picture
[https://static1.squarespace.com/static/57e561e720099e0d7a7f6aca/58276a5bf7e0ab81d3e577ae/589a5e20bf629ac702e0b122/1486596219084/Sideways.jpg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](url)

BarbourSmith, 2018-01-11:
In retrospect that is weird. Some routers have an adjustment knob on the side so the brackets are designed to work in both directions. As far as I know nobody has used that feature 🤷‍♂️

Closed 2018-01-15.

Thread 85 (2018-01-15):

Frame flex

BarbourSmith, 2018-01-15:
The stock frame has a measurable amount of flex in it which is becoming an important factor in calibration.

What is the easiest way to reduce the amount of flex in an existing frame while changing it the least amount?

blurfl, 2018-01-15:
I suggest a 10' 2x4 screwed to the arms just below the motor mounts as inexpensive and needing the fewest tools.

BarbourSmith, 2018-01-15:
Here is my first proposed solution:

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

It adds a 2x4 between the two arms. It requires an additional 2x4 and that the arm braces be re-cut, but no other changes are needed

BarbourSmith, 2018-01-15:
From playing with my current frame, there is some play between the motor mounts (the plywood which the motor is attached to) and the 2x4 that it is attached to. Is there any way to reduce play there? It seems like having both of the motors bolt directly to a long 2x4 is the best solution but a little bit harder to implement.

blurfl, 2018-01-15:
With  The motor mounts angled that way, there  could still be flex at the top of the work area. Turning them horizontal would allow you to screw them to the 10 foot 2 x 4, is that what you’re suggesting?

BarbourSmith, 2018-01-16:
I agree that we could still get flex at the top of the work area this way. I'm thinking that what we really want to do is what @dlang did where he moved the entire bar that the motors are on forwards so that the motors attach directly to the 2x4. I haven't thought of a way to do that which I really like yet

davidelang, 2018-01-16:
add a 10' 2x4 across the top connecting the wings. If you have the plywood  arm
covers, you can put the 2x4 in front of them and screw from the back.

This isn't the best new frame, but it's the quickest and easiest way to modify
an existing frame.

davidelang, 2018-01-16:
The best new frame is going to be very different from the best modification to an existing frame

modifying an existing frame is simply adding a 2x4, no need to modify the plywood parts

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

blurfl, 2018-01-16:
Adding the 2x4 in this manner helps brace the angled motor mounts as well - double win!

davidelang, 2018-01-16:
a top beam design that is similar to the original frame is
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

davidelang, 2018-01-16:
But I really like this folding, wheeled frame concept (and note that this makes it easy to move the top  bar forward)

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

all part of the onshape document at https://cad.onshape.com/documents/e635c24e358635f51da4b399/w/5a63b67113542f248fbe6d7b/e/50fff2211306b5f2bfa5dd3c

davidelang, 2018-01-16:
If we were willing to call a unistrut top beam the standard, we could have motor mounts made that would wrap around the strut and had a cap over the ends so that they were easily removable (with one bolt to hold them tight)

otherwise, you can just screw them to a 2x4.

Remember that the brackets don't have to be super strong, they need to support the weight of the top beam (~11 pounds for a 2x4) the sled (~20 pounds), the chain (~2 pounds), so call it ~25 pounds. That's not much and just about anything can do that without noticeable flex.

I didn't want to be screwing into the end-grain of the wood, so I already was planning for short lengths of 2x4 for the corners, so I just extended them to 12" long.

blurfl, 2018-01-16:
> call a unistrut top beam the standard

Before we do that we need to check in with users in other parts of the world... Steel strut might be hard to find and expensive outside the major urban areas of the US.

davidelang, 2018-01-16:
@blurfl

I agree, although unistrut is used for _so_ many things that it's probably available.

unfortunately, I can't figure out a good way to bend the material that would stay on the front of the material (so that it didn't care how deep it was)

blurfl, 2018-01-16:
@davidelang , I'm not sure I followed that...

davidelang, 2018-01-16:
2x4 is 1.5" thick, unistrut is 1  5/8" thick, pretty close to the same.

so if you have a motor mount that covered the bottom, end, front, and top of the beam, it would work with either unistrut or 2x material.

But I can't figure out something that's workable.

davidelang, 2018-01-20:
a note on the top beam attachment.

The alternate 1 design used a 2x10 on the top, with the idea that you can drill a series of holes in it and slide it forward an inch or two (a bit more if you use a 2x6 as the top board of the frame)

but a 2x10 is on the heavy side (heavier than a unistrut) and while this has some adjustability, it's not a lot.

So with the alternate 2 design, I extended the corner braces out so it doesn't depend on overlapping boards, which lets you use a unistrut or 2x4 for the top beam and move it to whatever distance you need. I made the supports 12", but it looks like 8-9" is about right for standard plywood.

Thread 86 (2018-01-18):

Wiki page claims 0.25in router bit but links to 0.1875in router bit.

abetusk, 2018-01-18:
The Wiki page for the [0.25in 2 Flute, Tungsten, Up Spiral Bit](https://github.com/MaslowCNC/Mechanics/wiki/0.25in-2-Flute,-Tungsten,-Up-Spiral-Bit) links to a bit sold on Home Depot that is in actuality a [0.1875in cut diameter](https://www.homedepot.com/p/Diablo-1-4-in-Up-Spiral-Router-Bit-DR75101/204073552).  The **Min Chuck Size Required** is `1/4 in.` but the **Cut Diameter** is `0.1875 in`.

I assume this bit should actually be a 0.25in cut diameter?  Could you please link to the proper router bit?

BarbourSmith, 2018-01-18:
Great catch! I vote we don't recommend that router bit at all anymore because there is a comparable one in our store for half the price. Although maybe it's a good idea to link to one that is available locally to most people. What does everyone think?

davidelang, 2018-01-18:
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

include both (with price/date fields that can be updated by users)

just listing ones you sell can leave a bad taste in people's mouth, even if it
is cheaper than the other one.

abetusk, 2018-01-19:
For people trying to build their own MaslowCNC, I think having a bill of materials that isn't tied to availability through the MaslowCNC's store front is a good idea.  Even if there's a primary link to the MaslowCNC's site with a secondary link to a comparable router bit on some other easily available site, maybe with a disclaimer, I think would be very beneficial.

People can decide for themselves whether they want to shop around for a cheaper or alternate router bit but providing a "known good" router bit helps in making that choice.  It's easier to tweak a known solution to an alternate solution than it is to create a solution from scratch.

abetusk, 2018-01-20:
Is this the actual bit that was used?

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

[0.25 in. x 1 in. Carbide Up Spiral Router Bit (2-flute, 0.25 in. chuck) ](https://www.homedepot.com/p/Diablo-1-4-in-x-1-in-Carbide-Up-Spiral-Router-Bit-DR75102/100660697)

If so, can we replace it in the Wiki?  There doesn't need to be a glowing recommendation to use this bit, but providing a link for a "known good" router bit goes a long way towards helping people trying to understand or assemble their own MaslowCNC.

BarbourSmith, 2018-01-22:
That looks like the right one. You are right that it's a good resource to keep, I agree with that reasoning

abetusk, 2018-01-23:
Wiki has been updated

BarbourSmith, 2018-01-23:
Excellent catch, excellent fix! 👍 👍 💯

Closed 2018-01-23.

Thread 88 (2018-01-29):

Broken link in wiki ("Z-Axis" page)

abetusk, 2018-01-29:
There is a broken link to a picture at the bottom of the [Z-Axis](https://github.com/MaslowCNC/Mechanics/wiki/Z-Axis) wiki page.

There is a picture of attaching a bungee cord to the router to take care of the slop and give more consistent cuts.  The picture was, as far as I can tell, originally posted to [the forum](https://forums.maslowcnc.com/t/z-axis-bungee-to-ensure-correct-depth/481).  There was a request to add it to the wiki, which was done, but the picture that was linked to has since rotted.

In general, maybe there should be a policy of linking, as much as possible, to pictures internal to the repo to avoid this type of link rot?  Could we add an 'img' folder somewhere so that the wiki can use that to point to images it needs?

BarbourSmith, 2018-01-29:
Great catch!

I've uploaded the image to the folder here: https://github.com/MaslowCNC/Mechanics/tree/master/Documentation

so the link will not break again. I agree that we should try to keep all our meda internal. I guess that would require pull requests to be made for pictures, but I think it's worth it

abetusk, 2018-01-29:
Thanks!

Closed 2018-01-29.

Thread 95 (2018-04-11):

Additions to Z-axis Kits

mrfugu, 2018-04-11:
Hey,

In running down the best solutions for reducing 'slop' in the Z-axis on the default system I think we have a list of materials well suited as additions to the Z-axis kit:

These are all low cost parts and readily available in quantity.

see: https://forums.maslowcnc.com/t/z-axis-only-moving-the-router-some-of-the-time/133/16?u=mrfugu

https://www.mcmaster.com/#91545a330
1-3x washers, used to remove slop from the bottom of the router screw in conjunction with retaining ring.

https://www.mcmaster.com/#98398a120
1-2x retaining ring, to replace/spares factory retaining ring, is possible to damage while placing washers.

https://www.mcmaster.com/#76445a743
12-18"x low friction tape. 3x router spindle body length. evenly spaced around router circumference

https://www.mcmaster.com/#12205t55
6x rubber bands. Works in conjunction with split-ring to apply down pressure on router in sleeve, between split ring and handle bolts.

https://www.mcmaster.com/#90905a659
1x split ring. sits on top of router head to hold rubber bands in place above router.

https://www.lowes.com/pd/Hillman-1-2-in-x-3-8-in-x-5-8-in-Nylon-Spacers/3012447
2x nylon spacers super glued on either side of router height adjustment flange. provides torsion stability to router part assembly:

 (640963002) Depth Interlock Lever
 (671758001) Depth Compression Spring
 (513396001) Depth Interlocking Lever Tab

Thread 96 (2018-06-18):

Flexible frame Concept

CMHinckley, 2018-06-18:
While it seems that there several posts asking if there are ways to make the operation of the Maslow CNC work in a more vertical orientation, it seems that a better solution might be to mount the frame directly to the wall with hinges at the top. The bottom would be pulled outward (and braced in this position for machining) and when machining is finished, the frame is rotated flat against the wall. This could eliminate a lot of framing, saving money, fabrication time and significantly reducing the storage space when the unit is not in use. Has anyone worked on a concept such as this, and would anyone like to work on such a solution?

The precision of the cnc machines can be influenced by dimensional changes caused by moisture and temperature fluctuations, the flatness of the bed, and the stiffness of the frame. It might be possible to increase the stiffness and stability of the frame by using a grid of 1"x 4" between 2 external layers (one front and one on back) of 1/4" hardboard sheets, which are flatter and cheaper than plywood. This composite frame could be formed by gluing and screwing parts together, and the screws could then be completely removed after the glue has set, eliminating every possibility of hitting a screw during machining. A sacrificial sheet, could be used in front of the machine frame to avoid damage to the frame when machining. Has anyone worked on a composite frame of this type, and would anyone like to work on such a solution?

davidelang, 2018-06-18:
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

you don't actually save that much, just the rear legs and kickers.

There are a number of people who have done this, and it workswell.

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

actually, most of the frame makes very little difference in the machine accuracy
(except if there is something that causes the sled to not slide, or the warpage
is bad enough to affect the Z depth)

The machine accuracy is almost entirely defined by how rigid the top beam is,
and how accurate the measurements during calibration are.

blurfl, 2018-06-18:
'''
mount the frame directly to the wall with hinges at the top.
'''
One of the beta testers, @Gero, built his fram this way, using a scissors jack to adjust the angle of the frame. It worked well for him.
'''
The precision of the cnc machines can be influenced by ... the flatness of the bed,
'''
I found this to be the case, the plywood I used for a workarea bowed and caused changes in the angle of the chain from the plabne of the sprocket. This would cause the chain to jump. It seemed to cause the sled to have additional frioction toward the sides of the workarea as well, but I don't have any data to prove it.

davidelang, 2018-06-18:
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

in your case this was inches worth of bowing to cause these problems

blurfl, 2018-06-18:
'''
in your case this was inches worth of bowing
'''
That's right. The composite frame that @CMHinckley suggests would be one way to prevent that kind of warping.

CMHinckley, 2018-06-18:
The max deflections of the top beam based on a total sled weight of approximately 17.5 lb (router, bricks, sled...) for the default frame is approximately 0.028" using Douglas Fir (Modulus of Elasticity of 1.8 million psi, and 2 x 4 framing). This includes the deflections resulting from the moment applied to the upright vertical members. This is a non-trivial portion of the target precision.  The best way to reduce the deflections is to increase the stiffness of the members and the bed.

blurfl, 2018-06-18:
That's true. Too, Doug fir is relatively strong but most users are using 'white-wood hem-fir' two-by lumber, which is less stiff and less stable.

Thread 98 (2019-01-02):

Different hardware than assembly guide/ videos

PoliciaMalo, 2019-01-02:
I finally got around to assembling my maslow cnc and there are hardware differences between the site instructions and what I received.

Is there an updated assembly guide for the new hardware?

Please...  I'm dying to finish assembly.

BarbourSmith, 2019-01-03:
Is the difference that you are missing the ring?

If that is the case I recommend using this linkage kit: http://maslowcommunitygarden.org/Maslow-triangulation-linkage-kit.html and then you can follow the normal instructions substituting the linkage for the ring. It will be a little bit more work, but you will get much better results than without the ring

PoliciaMalo, 2019-01-03:
No I have the ring kit and z axis.  It's hardware that I ran into after
mounting the motors

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

BarbourSmith, 2019-01-03:
hmmmm I am not sure what hardware that would be. Can you post a picture of what part it is?

PoliciaMalo, 2019-01-03:
Ahh ok I had to go to the instructions for the original design and the
parts were chain guides they changed the nails as well as added bushings
for the string pulleys.

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

BarbourSmith, 2019-01-05:
Excellent!

Can I ask how you ended up with the out of date instructions? Maybe I can
fix something to make them less confusing in the future.

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

PoliciaMalo, 2019-01-05:
The instructions on the website under the new default frame do not mention
the parts used in the old default frame.  Specifically the use of nails
instead of screws in the center bungee bearings, the use of nails now on
the center bearings instead of screws.  The small 2 inch plastil bearing
used in chain tension for the old default frame.  Etc.  I'll elaborate more
in the dorms when build complete.

Also the bungees seem too long compard to the photos in the new default
frame build.  I just ordered new bungee spool in case needed.

Thanks.

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

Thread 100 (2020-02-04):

Motor runs every time in same direction

mmmmmmmmmmmmmmm2, 2020-02-04:
Hi All please help me out, one of the motors is always running in the same direction, if i push up it goes up, if i push down it goes again up. and if i let it go to center it is every time somewhere else, and doesn't stop anywhere. what do i need to do...

JDogHerman, 2020-02-04:
Most likely the H-Bridge is dead on the controller card.

You could eliminate other remote possibilities that cabling  by swapping the Left and Right motor wires running to the card.

BarbourSmith, 2020-02-04:
I think this sounds like an encoder issue to me. If the motor can't read the encoder value it will always spin in one direction. What do you see happen when you press Actions -> Test motors / encoders?

mmmmmmmmmmmmmmm2, 2020-02-05:
Hi All,
tested the motors, it says testing L motor direction 1 Fail , direction 2 Fail, and that for L / R and Z
See attached photo, it is brand new, must be something i´m doing wrong

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

BarbourSmith, 2020-02-05:
Did you close the issue because you found the solution?

mmmmmmmmmmmmmmm2, 2020-02-06:
No i didn't, still not solve it ..

Pushed wrong button

Op wo 5 feb. 2020 23:14 schreef BarbourSmith <notifications@github.com>:

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

BarbourSmith, 2020-02-06:
Ok, let's figure out what is going on.

Do you see the motors move when running the test?

mmmmmmmmmmmmmmm2, 2020-02-07:
Hi all,

No, they do not move, when testing

But when i push manually it moves..

Op do 6 feb. 2020 23:34 schreef BarbourSmith <notifications@github.com>:

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

BarbourSmith, 2020-02-07:
Gotcha. When all three motors fail the test the issue is almost always with the power supply. Does the power supply have a blue light on it? Does the green light next to the plug come on when you plug the power supply into the controller board?

mmmmmmmmmmmmmmm2, 2020-02-07:
Good,

Correct, only two green lights.. no blue lights

Op vr 7 feb. 2020 07:14 schreef BarbourSmith <notifications@github.com>:

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

BarbourSmith, 2020-02-07:
Where are the the green lights? Are they both on the controller board? Can you post a picture of the controller board and the power supply?

mmmmmmmmmmmmmmm2, 2020-02-07:
See attached photos

One of controllerboard and of the adapter

Op vr 7 feb. 2020 17:36 schreef BarbourSmith <notifications@github.com>:

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

BarbourSmith, 2020-02-07:
I don't think the photos actually attached 😢

mmmmmmmmmmmmmmm2, 2020-02-08:
Mmmm, strange..

Will send them in 2 emails

Op vr 7 feb. 2020 23:01 schreef BarbourSmith <notifications@github.com>:

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

mmmmmmmmmmmmmmm2, 2020-02-08:
Number 2

Op vr 7 feb. 2020 23:01 schreef BarbourSmith <notifications@github.com>:

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

davidelang, 2020-02-08:
they did not come through, try adding them through the web interface.

David Lang

mmmmmmmmmmmmmmm2, 2020-02-09:
Okay, here they are
![Uploading 20200207_175711.jpg…]()

BarbourSmith, 2020-02-09:
I'm still not seeing the picture :(

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

Let's move this conversation into the forums...I think we'll have less technical trouble there, you will get faster responses from more people, and that is really the right place for the conversation since this is about solving a particular issue instead of proposing a change to the design of the machine

BarbourSmith, 2020-02-09:
The forums are https://forums.maslowcnc.com/. You can login with your github login so no need to make an account or anything

mmmmmmmmmmmmmmm2, 2020-02-09:
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
First

mmmmmmmmmmmmmmm2, 2020-02-09:
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
Second photo

BarbourSmith, 2020-02-09:
Nice! Ok everything looks good there. And we are still seeing the motor move when you manually command them to move, but no movement at all during the test?

mmmmmmmmmmmmmmm2, 2020-02-09:
Yes, no movement during test, but can do manual but always same direction

BarbourSmith, 2020-02-09:
This is totally like anything I have seen before. The test should be overriding the controls in a way which makes the motor move if it has power...but the pictures and the fact that you can manually move it mean we have power

BarbourSmith, 2020-02-09:
Is the behavior the same on all the motors? The only thing I can think could be a bad connection in one of the connectors. Maybe let's try unplugging them all and re-plugging each motor very firmly

mmmmmmmmmmmmmmm2, 2020-02-09:
Strange isn't? Is an idea to set up software again?

BarbourSmith, 2020-02-09:
So strange 😲

It could be worth setting up the software again, but this feels like a hardware issue to me

BarbourSmith, 2020-02-09:
I think checking the connections on the cables is the best place to start. I would unplug each motor and re-plug them firmly

mmmmmmmmmmmmmmm2, 2020-02-09:
It is new bought it end December , coming 2 weeks i'm not near my cnc, if you have any suggestions please let me know

BarbourSmith, 2020-02-09:
Did you try unplugging and re-plugging the cables to the motors?

Have you contacted MakerMade? Do they have any suggestions?

mmmmmmmmmmmmmmm2, 2020-02-09:
Haven't tried to switch the motors but tried several times the connection. Have no idea who to contact assume there is some kind of warranty..

BarbourSmith, 2020-02-09:
They should send you a free replacement for anything which is not working...the tricky thing is I'm not even sure what to ask them for because I'm not sure what is going on. Maybe ask for a new arduino and controller board to be safe?

You can find them in the forums by posting your issue and tagging them as @makermadecnc they usually respond there pretty quickly

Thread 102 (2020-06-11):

Initial plunge off path

DJscreen, 2020-06-11:
We are cutting designs into 6x4 sheets of 6mm ply. The designs are 6" x 6" max and the cutouts are removed to create a lattice effect. There are two of the designs where the initial plunge through the material is about 2 mm off leaving noticeable "dings". We intend to experiment with 2 mm tabs at the relevant places and by inserting bulges into the svgs which will be manually finished later.

The panel svg was set up using Inkscape v9 and the nc file generated in Krabzcam which as far as I can see is an excellent replacement for Makercam

BarbourSmith, 2020-06-12:
Hmmmm my first instinct is that this could be play in the router. Which type of z-axis are you using?

Another possible option is to add a lead in to your cuts which makes it so that the router bit doesn't raise and lower right along the edge of the part like this:

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

I am not familiar with Krabzcam, but I know CamBam supports it and they have a free trial version that might be worth playing with

DJscreen, 2020-06-20:
Thanks for your suggestions. We may have solved it by plunging the bit half way through the ply, withdrawing to safe height and then plunging to final depth. We have been using a 6mm twin flute cutter and maybe it is too stressed plunging the full depth in one go.

BarbourSmith, 2020-06-20:
That makes total sense. Nice problem solving!

On Sat, Jun 20, 2020, 2:27 PM David Johnston <notifications@github.com>
wrote:

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

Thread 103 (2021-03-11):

Chain pull on setup.

alaskanalain, 2021-03-11:
On setup, the "measure chain" step kept pulling the chain until it stretched, the arms bent a lot and the motor eventually started to pull loose, if I didn't stop it I assume the motor would have burned out or torn loose. I beefed up the machine and now it's built like a tank.
With the other chain, as before, I manually pulled the chain so there was a bit of slack then started to measure again, following instructions exactly, but it still bent the arms. It stopped and went slack as it should but not in time, so now the other chain is stretched too.  Both chains now skip on the teeth every time I try to do the test cut.  One tooth is slightly chipped too as a result (not too bad).  I have chain guides but it still slips due to the stretch.  The motors simply did not turn off and slack when they should.  The many youtube videos I watched have confirmed this.

I am reasonably good with machines but this has me near tears after many hours.  **Can I please get some new chains**, this time I will just use a tape measure, the measurements from the machine pulling them tight didn't yield accurate results either.

I went through the setup many times since and looked at this from every angle and don't think it's something I did wrong.  I have a small CNC and had no trouble with that at all.  Bicycle chains stretch and those are thicker than this, I assume that is why others also sometimes have issues with skipping.
Please help, Thank you
Alain

BarbourSmith, 2021-03-11:
I couldn't agree more that the calibration process is confusing and very much needs to be improved.

Which version of the kit are you using (ie who did you buy it from)? The chains and gears should be strong enough to handle the forces involved easily so I would be somewhat suspect of the build quality.

Which software are you using for calibration? WebControl or GroundControl?

alaskanalain, 2021-03-11:
Ground control and I think the seller was "Maker Made".  I got the kit with Z control, not sure what model, etc. It's one of the newer ones probably, got it a few months ago.
It's well made but the motors didn't want to stop pulling, they did eventually but I don't think it should pull that hard, definitely straining every component, I could hear the creaking and motor strain sounds.
I don't think the chains are made for that, far less beefy than my chainsaw and yet the chainsaw chain stretches on first use, it's designed with that in mind, Bicycles too.
Thanks for that, any ideas?  Do I have to buy new chains? Can I just measure the machine?  I am not even sure where the test cut should be on the plywood.

BarbourSmith, 2021-03-12:
I believe that they have their own software that might work better for you than Ground Control. I believe it's called Makerverse? Ground is pretty out of date at this point.

You can manually measure, but it isn't usually accurate enough.

Maker Made (https://makermade.com/) would be the people to get in touch with if you want some new chains.

alaskanalain, 2021-03-12:
Thank you

On Fri, Mar 12, 2021 at 8:48 AM BarbourSmith ***@***.***>
wrote:

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

BarbourSmith, 2021-03-13:
Of course, although I don't know if I really helped much :)

For better help come hang out in the forums:
https://forums.maslowcnc.com/

You can probably find someone with a similar experience there who might have some insights.

Closed 2021-03-13.

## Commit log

2014-11-17 Case Added
2014-11-17 Files Added
    [Bed.DXF, Sheet1.DXF, Sheet2.DXF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]
2014-12-10 Added extra dremel mounts
    [ExtraBrackets.DXF]
2015-01-20 Changed file names to be more clear
    [MDFBasePlate.DXF, MDFPartsSheet1.DXF, MDFPartsSheet2.DXF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]
2016-10-09 Add Maslow CAD files
    [ExtraBrackets.DXF, MDFBasePlate.DXF, MDFPartsSheet1.DXF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]
2016-11-03 Added BOM
2016-11-03 update BOM
2016-11-03 Updated BOM
2017-01-01 move mounting holes
    [Machine.skp]
2017-01-18 sled re-design
    [Sled.skp]
2017-01-30 backups saved
    [Sled.skp]
2017-02-17 move motors forward 25mm
2017-02-17 extend motor mounts
    [Machine.skp]
2017-02-17 update hole spacing and size
    [Machine.skp]
2017-03-15 Fix motor mount and add files for angle braces
2017-03-16 make motor mount lines thin
2017-03-17 add legs diagram
2017-03-17 add how to cut 2x4 picture
2017-03-20 make mounting holes larger
    [Sled.skp, TempSeld.skp]
2017-03-20 add temp sled
    [TempSeld.skp]
2017-03-21 add mounting holes with room for counter sink and regenerate PDF
2017-03-21 true up crosses and add brick holder
    [TempSeld.skp]
2017-03-21 new cad files with full page used
2017-03-22 commit to switch branches
    [TempSeld.skp]
2017-03-24 put parts in order and switch inches to fractions
2017-03-29 Add hardware CAD models, organize
    [Bracket A.skp, Bracket B.skp, Bracket C.skp]
2017-03-30 regenerate temp sled svg
    [TempSeld.skp]
2017-03-30 remove brick holder part
    [TempSeld.skp]
2017-03-31 Update pictures for cutting frame
2017-04-14 Add picture of alternative frame
2017-04-17 Add a test shape to measure calibration
    [Test Shape.skp]
2017-04-18 Change test shape file name
    [6 Inch Square Test Shape.skp]
2017-04-20 Add picture of tuning calibration
2017-04-22 Forgot to include a second set of braces
    There are two legs. Duh
2017-04-24 Add missing motor mount to all parts laid out
2017-04-25 Add pictures of cut parts
2017-04-26 Add CAD pictures
2017-04-28 Add more photos for assembling the final frame
2017-04-29 Update leg diagram picture
2017-04-30 Add pictures for installing z-axis instructions
2017-04-30 Add attach bricks picture
2017-05-07 Add new machine design
    [New Machine Design.skp]
2017-05-07 Make dimensions more regular
    [New Machine Design.skp]
2017-05-09 Update design
    [New Machine Design.skp]
2017-05-10 update design file
    [New Machine Design.skp]
2017-05-12 Add new arm shape
2017-05-14 Add cut list for boards
    [New Machine Design.skp]
2017-05-29 Update motor specs
2017-06-18 Create All_Parts_via_Fusion360.txt
    Concept: to allow a new MaslowCNC user to easily begin working with Fusion360 by providing a 'comprehensive' Project file that includes extrusions for all machinable parts, discreet cutting paths, an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
2017-06-21 Change sketchup file names
    [Machine.skp, New Machine Design.skp, Old Machine Design.skp]
2017-06-21 Rounded the pointy ends of NewArmShape.svg
    Added a 3mm fillet to the pointy ends of the NewArmShape. (Via Fusion360, exported to Ai as .dxf, then exported to .svg)
2017-06-21 edit NewArmShape + allow 1/4" bit
    I rounded the pointy ends of the NewArmShape, and slightly widened (from 6 to 7mm) the Brick Holder mounting holes, in order to allow a 1/4" (6.4mm) bit to attempt to drill them. Fusion360 wasn't hap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
2017-06-28 Replacing invalid files
    I'm not sure why these appear as 'invalid' in the current version. The File size is significantly different from my local copies, so I'm reposting them via this pull req.
2017-07-02 Update CAD files
    [Machine.skp, Maslow Frame.step, Maslow Frame.stl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]
2017-07-03 Update final frame steps 1-8
2017-07-07 Updated to latest SVGs, new URL
    Rebuilt using the latest SVGs.
    New URL for Fusion360 Cloud project.
    Fusion360 File also incorporates the following changes:
    New GRBL PostProcessor
    Advanced tool paths for pocket cuts, and engraved angle braces.
    Refined Tool Settings and Tolerances.
2018-02-13 Add picture of bolt together frame
2018-02-15 Add cut list and drill list files
2018-02-15 add photos of cut parts
2018-02-15 Add pictures of holes drilled
2018-02-16 Add plywood spacers pictures
2018-02-17 add sprockets picture
2018-02-20 launch calibrate pic
2018-02-28 Add picture of cutlist for default frame
2018-03-01 add default frame CAD overview
2018-03-01 add photos for default frame
2018-03-02 update CAD drawing overview picture
2018-03-02 Update Cut List
2018-03-02 add picture of 2x4s cut
2018-03-02 add pictures through the legs
2018-03-03 Add pictures of frame built
2018-03-03 update CAD pictures
2018-03-03 update cut list with shorter motor protrusion
2018-03-07 Update CAD drawing images with latest design
2018-03-07 extend ledge to rest wood on .25 in
2018-03-08 update cut 2x4s picture
2018-03-08 update CAD images
2018-03-23 add bom and instructions
2018-04-04 Shorten top beam by 1"
    See discussion here:
    https://forums.maslowcnc.com/t/sun-with-face-new-stock-frame-design-sun-with-face/2025/926
